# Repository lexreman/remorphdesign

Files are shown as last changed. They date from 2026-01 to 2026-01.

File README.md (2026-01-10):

<div align="center">
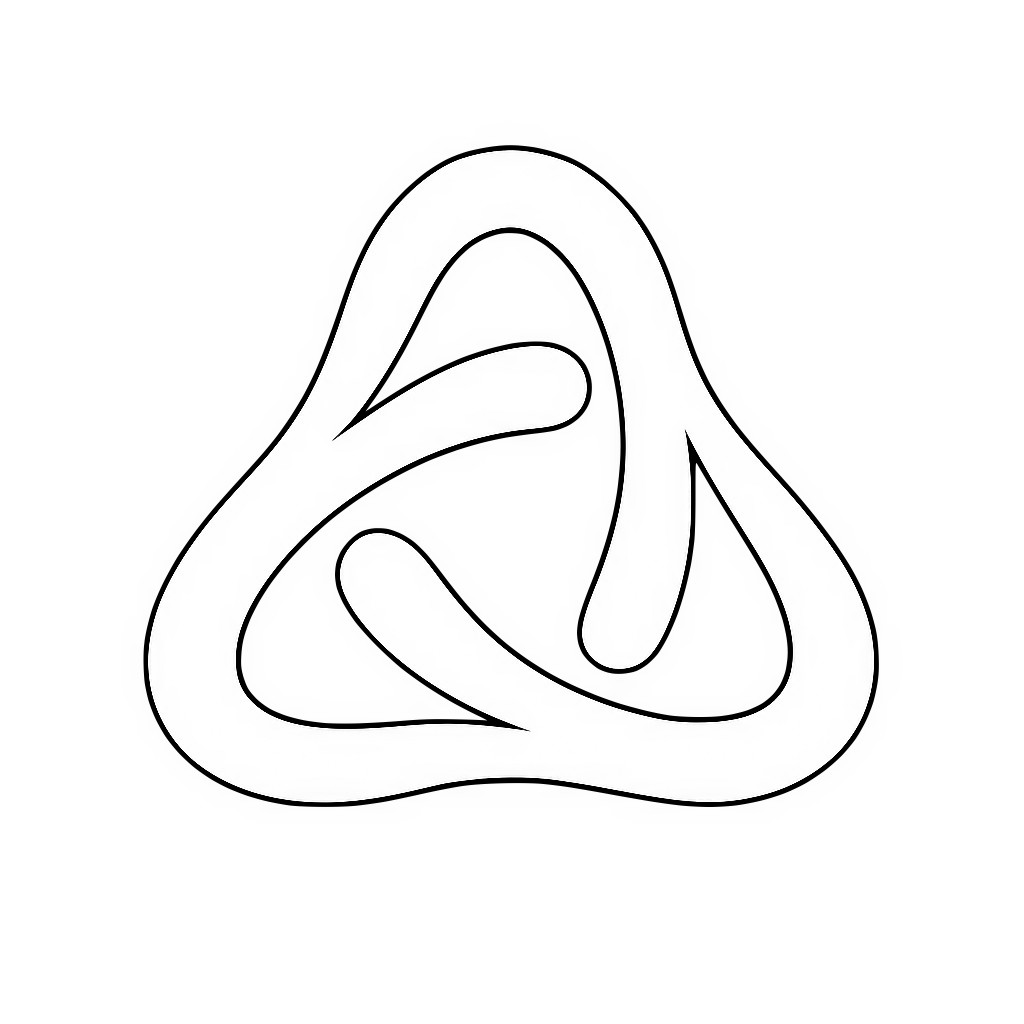
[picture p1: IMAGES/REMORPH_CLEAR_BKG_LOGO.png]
Remorph Logo


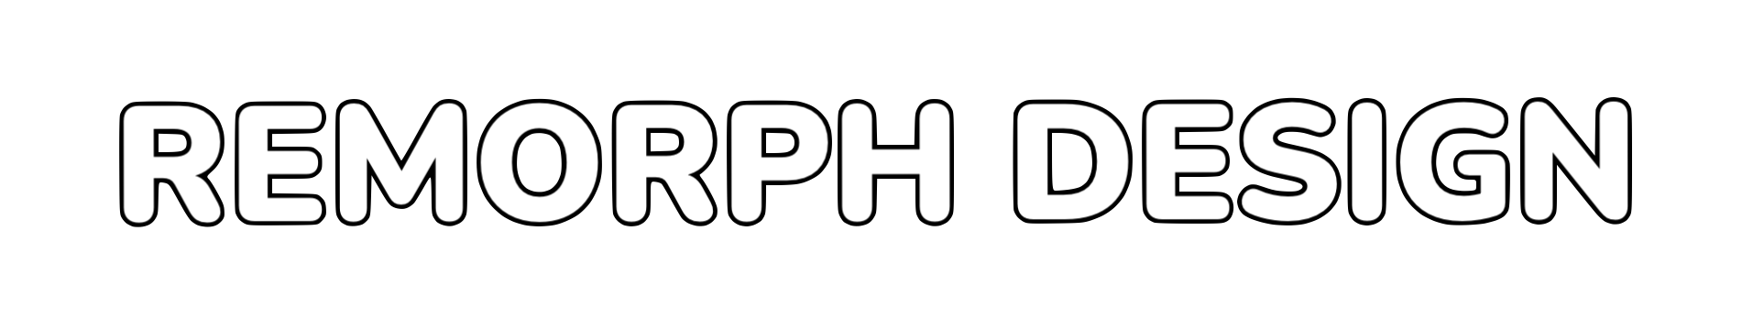
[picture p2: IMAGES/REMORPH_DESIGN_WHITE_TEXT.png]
Remorph Design Text


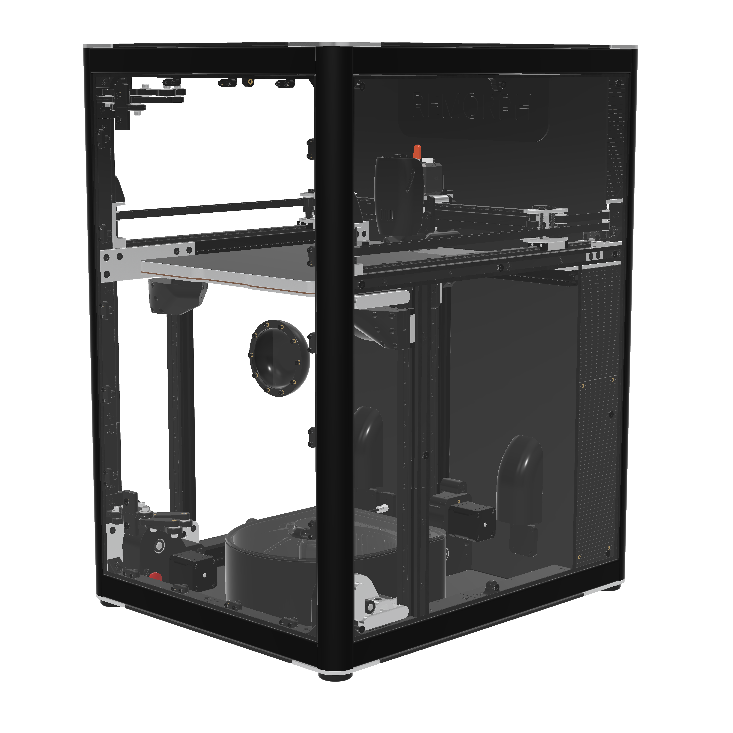
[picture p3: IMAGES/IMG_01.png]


</div>

* CPAP for print cooling and chamber convection 

* HEPA and carbon pellets with top-down convection 

* Static core XY 

* Frame made of 3030s and 2020s T-slot extrusions 

* Nearly all mechanical parts are machined aluminum 

* 48V N23 servos for X and Y 

* Servos and electronics isolated 

* 9mm belts for X Y Z 

* 12mm linear rails 

* 5:1 gear ratio for Z 

* Maxwell kinematic couplers 

* X307 Y307 Z304mm 

* W460 D560 H720mm 

* Hinges, door handle and connected cables are all internal 

* 4mm panels 

* Sealed internal filament dry box 

* External filament feed possible 

* Optical endstops 

* All idlers and gears use 5mm shafts with 13mm bearings 

* Nozzle wiper with a slide-out bucket

  **For more details, visit [www.remorphdesign.com](https://www.remorphdesign.com)**

  

<div style="display: flex; gap: 2%; flex-wrap: wrap; justify-content: flex-start;">
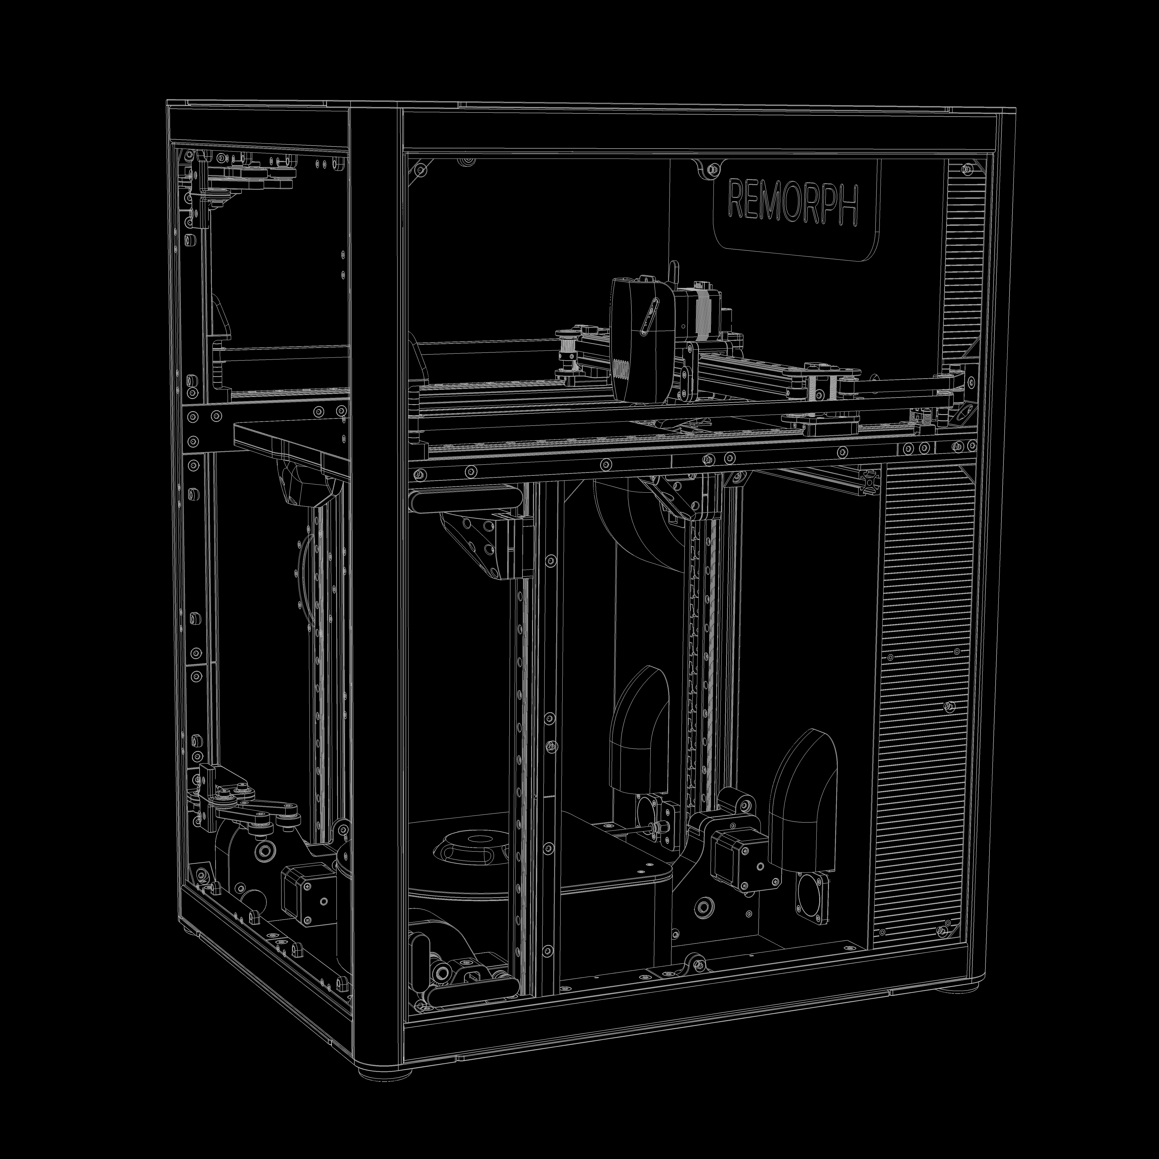
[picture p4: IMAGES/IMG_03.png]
  
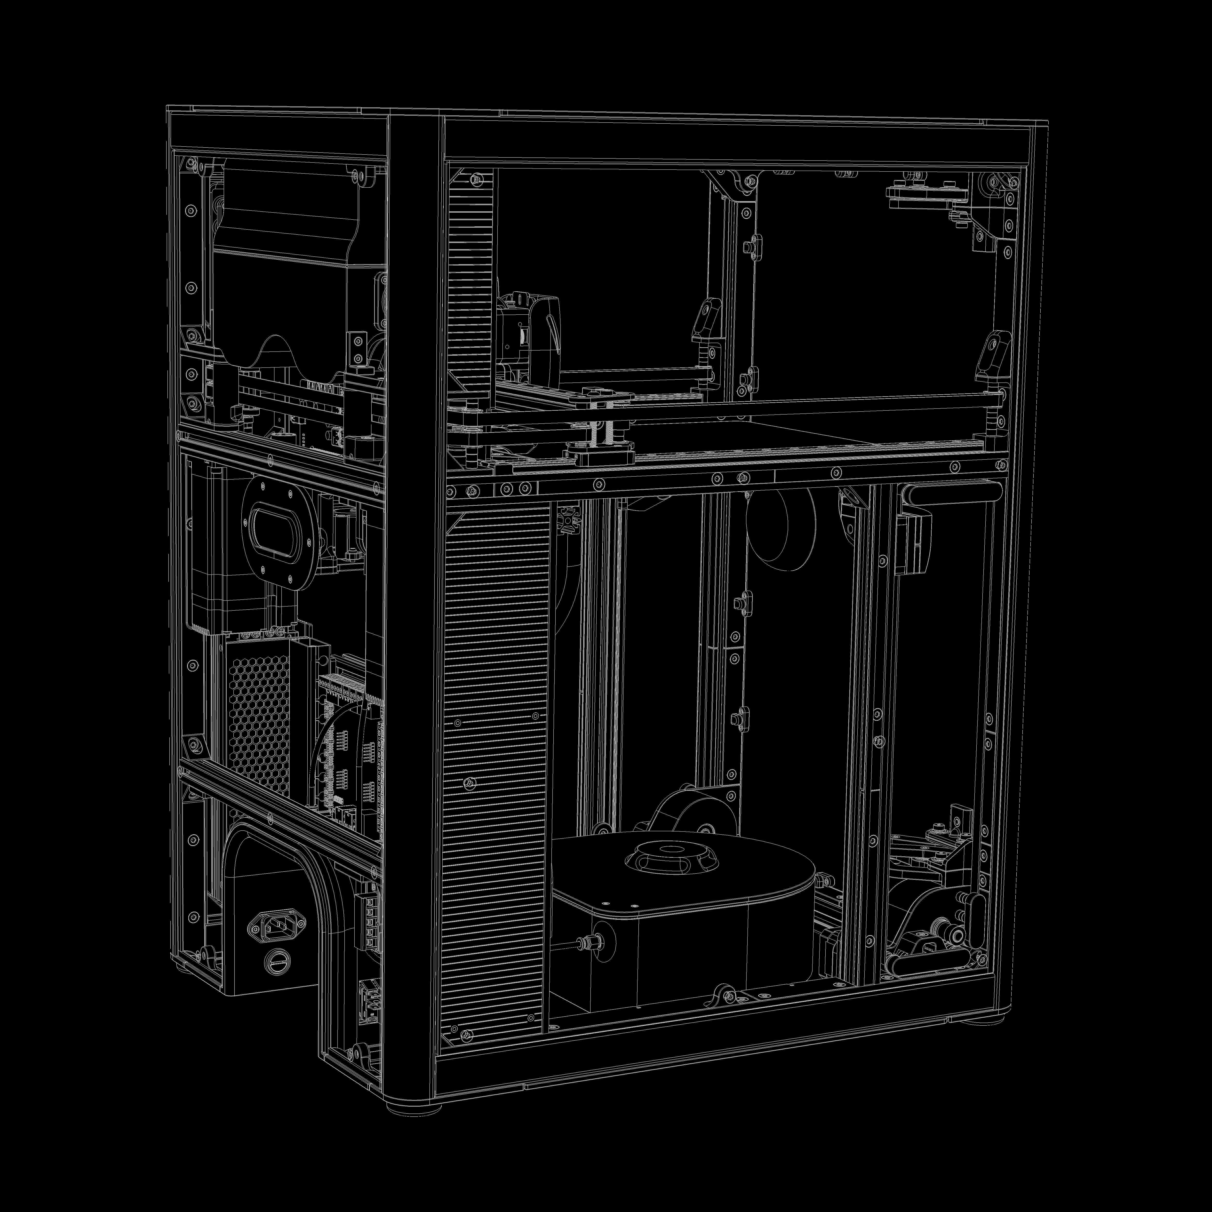
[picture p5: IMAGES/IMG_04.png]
  
</div>

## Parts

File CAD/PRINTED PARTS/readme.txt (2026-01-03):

 
 
—————————————————————————————————————————————————————————————————————— 

 1: All printed parts can fit on 250x250 plate. 
 
 2: Real ASA-CF or better, such as PPS-CF is recommended. 
 
 3: Some parts need considerably more perimeters and infill percentage. 
 
 4: Some parts have been designed with infill as filters. 
 
 5: Some parts require excellent short bridges capabilities. 
 
 6: Very few parts require support. 
 
 7: For great aesthetics, check cad assembly for part orientation, 
    and paint seam at unlikely seen position once installed. 

 ——————————————————————————————————————————————————————————————————————

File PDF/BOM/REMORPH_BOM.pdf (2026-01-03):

# REMORPH DESIGN

# BILL OF MATERIALS

## V_BETA_JAN26

FASTENERS: SCREWS
1 | M2.5x8 Tapping Pan Torx | 6
2 | M3x8 Socket Hex Stainless Steel Black | 50
3 | M3x40 Socket Hex Stainless Steel Black | 4
4 | M3x6 Button Torx Stainless Steel Black | 26
5 | M3x10 Button Torx Stainless Steel Black | 25
6 | M3x14 Button Torx Stainless Steel Black | 24
7 | M3x20 Button Torx Stainless Steel Black | 15
8 | M3x6 Flat Torx Stainless Steel Black | 54
9 | M3x10 Flat Torx Stainless Steel Black | 214
10 M3x14 Flat Torx Stainless Steel Black | 37
11 | M3x20 Flat Torx Stainless Steel Black | 26
12 M3x30 Flat Torx Stainless Steel Black | 7
13 | M3x45 Flat Torx Stainless Steel Black | 14
14 M4 ⌀5x10 Shoulder Screw | 14
15 | M5x10 Headless Hex | 2
16 M5x20 Hex Bolt Stainless Steel Black | 2
17 | M5x12 Socket Hex Stainless Steel Black | 8
18 M5 ⌀6x55 Shoulder Screw | 4
19 | M5x8 Button Torx Stainless Steel Black | 24
20 M5x10 Button Torx Stainless Steel Black | 56
21 | M5x14 Button Torx Stainless Steel Black | 14
22 M5x40 Button Torx Stainless Steel Black | 11
23 | M5x8 Flat Torx Stainless Steel Black | 20
24 M5x10 Flat Torx Stainless Steel Black | 156
25 | M5x12 Flat Torx Stainless Steel Black | 98
26 M5x14 Flat Torx Stainless Steel Black | 9
27 | M5x20 Flat Torx Stainless Steel Black | 6
28 M5x25 Flat Torx Stainless Steel Black | 6
29 | M5x35 Flat Torx Stainless Steel Black | 8
30 M5x40 Flat Torx Stainless Steel Black | 2
31 | M6x12 Flat Torx Stainless Steel Black | 2
32 M8 to M5 Adapter 15mm | 8
33 | M8x40 Button Torx Stainless Steel Black | 2

REMORPH B.O.M. PAGE 1 OF 4

FASTENERS: WASHERS
34 | M3x6x1 Washer Stainless Steel Black | 52
35 M5x8x0.5 Washer Stainless Steel | 8
36 | M5x8x1 Washer Stainless Steel | 90
37 M6x10x1 Washer Nylon | 20
38 | M8x16x2 Washer Steel or Aluminum Black | 14
FASTENERS: SPACERS
39 | M5x8x4 Round Spacer Black | 56
40 M5x8x5 Round Spacer Black | 27
FASTENERS: STANDOFFS
41 M3 (Tap) ⌀5x20 Standoff | 4
42 | M3 (Tap) ⌀5x25 Standoff | 8
43 M5 (Tap) ⌀8x80 Standoff | 1
FASTENERS: HEAT-SET INSERTS
44 M3x5x5 Heat Insert | 334
45 | M4x7x5 Heat Insert | 28
46 M5x8x6 Heat Insert | 22
47 | M6x9x6 Heat Insert | 6
FASTENERS: NUTS
48 | M5x2.7 Hex Nut | 1
49 M3 2020 T-Nut | 50
50 | M5 BS20 T-Nut | 32
51 M5 2020 T-Nut | 87
52 | M5 BS30 T-Nut | 24
53 M5 3030 T-Nut | 202
FRAME: JOINTS
54 90º 2020 Corner Joint | 42
FRAME: EXTRUSIONS
55 2020 T-Slot 200mm | 2
56 | 2020 T-Slot 400mm | 6
57 2020 T-Slot 450mm | 1
58 | 2020 T-Slot 500mm | 2
59 3030 T-Slot 400mm | 1
60 | 3030 N1 T-Slot 400mm | 3
61 3030 N1 T-Slot 500mm | 4
62 | 3030R T-Slot 700mm | 4

MOTION: BEARINGS
63 | Ball Bearing F698 | 11
64 Ball Bearing 695 | 43
65 | Ball Bearing F695 | 90
MOTION: SHAFTS
66 | 5x20 Shaft | 5
67 5x25 Shaft | 15
68 | 5x35 Shaft | 3
69 5x40 Shaft | 10
70 | 5x65 Shaft | 6
71 8x65 Shaft with Flat Side (D Type) | 5
MOTION: LINEAR RAILS
72 MGN12H 400 | 4
73 | MGN12H 450 | 2
MOTION: GEARS
74 | 2GT 16T B5 Pulley for 9mm Belt | 3
75 2GT 20T B5 Pulley for 9mm Belt (Black) | 2
76 | 2GT 20T B8 Pulley for 9mm Belt (Black) | 5
77 2GT 80T B8 Pulley for 9mm Belt | 3
MOTION: BELTS
78 9mm 2GT3 6897mm (8000mm Recommended) | 1
79 | Closed Loop 9mm 2GT2 210mm | 3
MOTION: SHAFT COUPLERS
80 | GND GTC 19x26 8x8 or 8 to 8mm Shaft Coupler (⌀21x31mm MAX) | 2
MOTION: BALL JOINTS
81 | M5 12mm Magnetic Steel Ball | 3
MOTORS
82 | OMC ISV57T-180S or N23 146mm MAX | 2
83 N17 48 or 60mm MAX | 3
ELECTRONICS: FANS
84 ASB02505SHA-AY6B or 10x25mm Axial Fan | 1
85 | WS7040-24 with controller | 2
86 9BMC24P2G001 | 1
ELECTRONICS: POWER SUPPLIES
87 LCW15US05 | 1
88 | UHP-500-24 | 1
89 UHP-500-48 | 1

ELECTRONICS: CONNECTORS
90 | Degson 6p Set 15EDGKM-3.81-06P + 15CDGV-3.81-06P | 9
91 Wago 221-415 | 3
92 | AC Inlet IEC 320-C14 15GEEG3E | 1
93 Fuse Holder SCHURTER 0031.2207 | 1
ELECTRONICS: SWITCHES
94 Rocker Switch Bulgin C6050ALBR-1197W | 1
95 | 16mm Panel Flat Push Button | 1
96 16mm Red Mushroom Button | 2
ELECTRONICS: SENSORS
97 M3 PT1000 | 3
98 | OPTEK OPB990T51Z | 2
99 BEACON LP | 1
100 | BME680 Adafruit 3660 | 1
101 BTT SFS 2 | 1
ELECTRONICS: PCBS
102 Recore A8 | 1
103 | BTT EBB42 | 2
104 RPI USB 3.2 HUB HAT | 1
105 | Matek Mini Hub | 1
MISCELLANEOUS
106 | TE Connectivity Potter SSRMP-240D16R | 2
107 LED COB 24V 7W ⌀20mm | 1
108 | PC4-M6 | 7
109 3x5mm 2.3m EVA Strip (3m Recommended) | 1
110 | 1x5mm 20.2m EVA Strip (22m Recommended) | 1
111 ⌀6mm Sealing Rope 820.4mm (vacuum table) | 1
112 | CPAP Tube | 2
113 ⌀40x10 Rubber Foot | 4
114 | Filament tube 2m | 1
115 3x10x20mm Rubber for Nozzle Wipper | 1
116 | 20x40x300mm Raceway | 1
117 Nema 17 Rubber Damper 2mm | 6
118 | 10x15x25 Magnet | 3
119 ⌀5x5 Magnet | 100
120 | Printed Parts | ?
121 Milled Parts | 54
122 | PC/CF Panels | 10

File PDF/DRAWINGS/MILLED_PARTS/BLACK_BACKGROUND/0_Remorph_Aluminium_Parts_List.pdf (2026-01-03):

### REMORPH ALUMINIUM PARTS LIST

1 TCP: Top Corner Plate | 7075-T6 | 5x73x73 | 4
2 | FBCP: Front Bot Corner Plate | 7075-T6 | 5x73x73 | 2
3 LBBCP: Left Bot Back Corner Plate | 7075-T6 | 10x50x103 | 1
4 | RBBCP: Right Bot Back Corner Plate | 7075-T6 | 10x50x103 | 1
5 LFZDM: Left Front Z Drive Mount | 7075-T6 | 5x97x155 | 1
6 | RFZDM: Right Front Z Drive Mount | 7075-T6 | 5x97x155 | 1
7 FTBZIM: Front Top Big Z Idler Mount | 7075-T6 | 5x41x155 | 2
8 | XYP: XY Plate | 7075-T6 | 5x139x450 | 1
9 FTLZIB: Front Top Little Z Idler Body | 7075-T6 | 8x15x89 | 2
10 | FZTB: Front Z Tensioner Body | 7075-T6 | 21x27x42 | 2
11 FBBZIB: Front Bot Big Z Idler Body | 7075-T6 | 15x25x76 | 2
12 | FBLZIB: Front Bot Little Z Idler Body | 7075-T6 | 8x15x45 | 2
13 LBZDM: Left Back Z Drive Mount | 7075-T6 | 9x54x94 | 1
14 | RBZDM: Right Back Z Drive Mount | 7075-T6 | 9x54x94 | 1
15 BZTB: Back Z Tensioner Body | 7075-T6 | 16x22x28 | 1
16 | BZPP: Back Z Puller Plate | 7075-T6 | 5x16x30 | 1
17 BZIM: Back Z Idler Mount | 7075-T6 | 25x29x75 | 1
18 | XYBTM: XY Bot Tensioner Mount | 7075-T6 | 5x69x112 | 2
19 XYTTM: XY Top Tensioner Mount | 7075-T6 | 5x65x112 | 2
20 | FZYTLB: First XY Tensioner Lever Body | 7075-T6 | 5x24x94 | 2
21 SXYTLB: Second XY Tensioner Lever Body | 7075-T6 | 5x24x94 | 2
22 | XYTPB: XY Tensioner Puller Body | 7075-T6 | 15x23x30 | 2
23 TBB: Tensioner Bracket Body | 7075-T6 | 4x22x80 | 2
24 | LYSB: Left Y Stopper Body | 7075-T6 | 9x28x35 | 2
25 RYSB: Right Y Stopper Body | 7075-T6 | 9x28x35 | 2
26 | LXYIM: Left XY Idler Mount | 7075-T6 | 23x25x58 | 1
27 RXYIM: Right XY Idler Mount | 7075-T6 | 23x25x58 | 1
28 | LBXYJB: Left Bot XY Joint Body | 7075-T6 | 10x54x60 | 1
29 RBXYJB: Right Bot XY Joint Body | 7075-T6 | 10x54x60 | 1
30 | LMXYJB: Left Middle XY Joint Body | 7075-T6 | 18x20x32 | 1
31 RMXYJB: Right Middle XY Joint Body | 7075-T6 | 18x20x32 | 1
32 | TXYJB: Top XY Joint Body | 7075-T6 | 4x24x62 | 2
33 TP: Toolhead Plate | 7075-T6 | 9x66x99 | 1
34 | LM: LED MOUNT | 7075-T6 | 10x50x75 | 1
35 RRTM: RAPIDO REMORPH Toolhead Mount | 7075-T6 | 5x43x43 | 1
36 | CRTS: CHUBE REMORPH Toolhead Spacer | 7075-T6 | 2x26x26 | 1 Total 54

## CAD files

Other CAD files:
CAD/ASSEMBLY/REMORPH_DESIGN_BETA_1.step
CAD/MILLED PARTS/13_Left_Back_Z_Drive_Mount.step
CAD/PC PANELS/8_Back_Panel.step
CAD/MILLED PARTS/5_Left_Front_Z_Drive_Mount.step
CAD/PC PANELS/10_Filament_Dry_Box_Lid.step
CAD/MILLED PARTS/27_Right_XY_Idler_Mount.step
CAD/PC PANELS/5_Top_Panel.step
CAD/MILLED PARTS/12_Front_Bot_Little_Z_Idler_Body.step
CAD/PC PANELS/4_Rear_Connectors_Recess_Panel.step
CAD/MILLED PARTS/17_Back_Z_Idler_Mount.step
CAD/PC PANELS/1_Inside_Bot_Panel.step
CAD/MILLED PARTS/29_Right_Bot_XY_Joint.step
CAD/PC PANELS/7_Right_Panel.step
CAD/MILLED PARTS/3_Left_Bot_Back_Corner_Plate.step
CAD/PC PANELS/2_Inside_Top_Panel.step
CAD/MILLED PARTS/18_XY_Bot_Tensioner_Mount.step
CAD/PC PANELS/9_Front_Panel.step
CAD/MILLED PARTS/30_Left_Middle_XY_Joint_Body.step
CAD/ASSEMBLY/REMORPH_DESIGN_BETA_1.x_t
CAD/MILLED PARTS/10_Front_Z_Tensioner_Body.step
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

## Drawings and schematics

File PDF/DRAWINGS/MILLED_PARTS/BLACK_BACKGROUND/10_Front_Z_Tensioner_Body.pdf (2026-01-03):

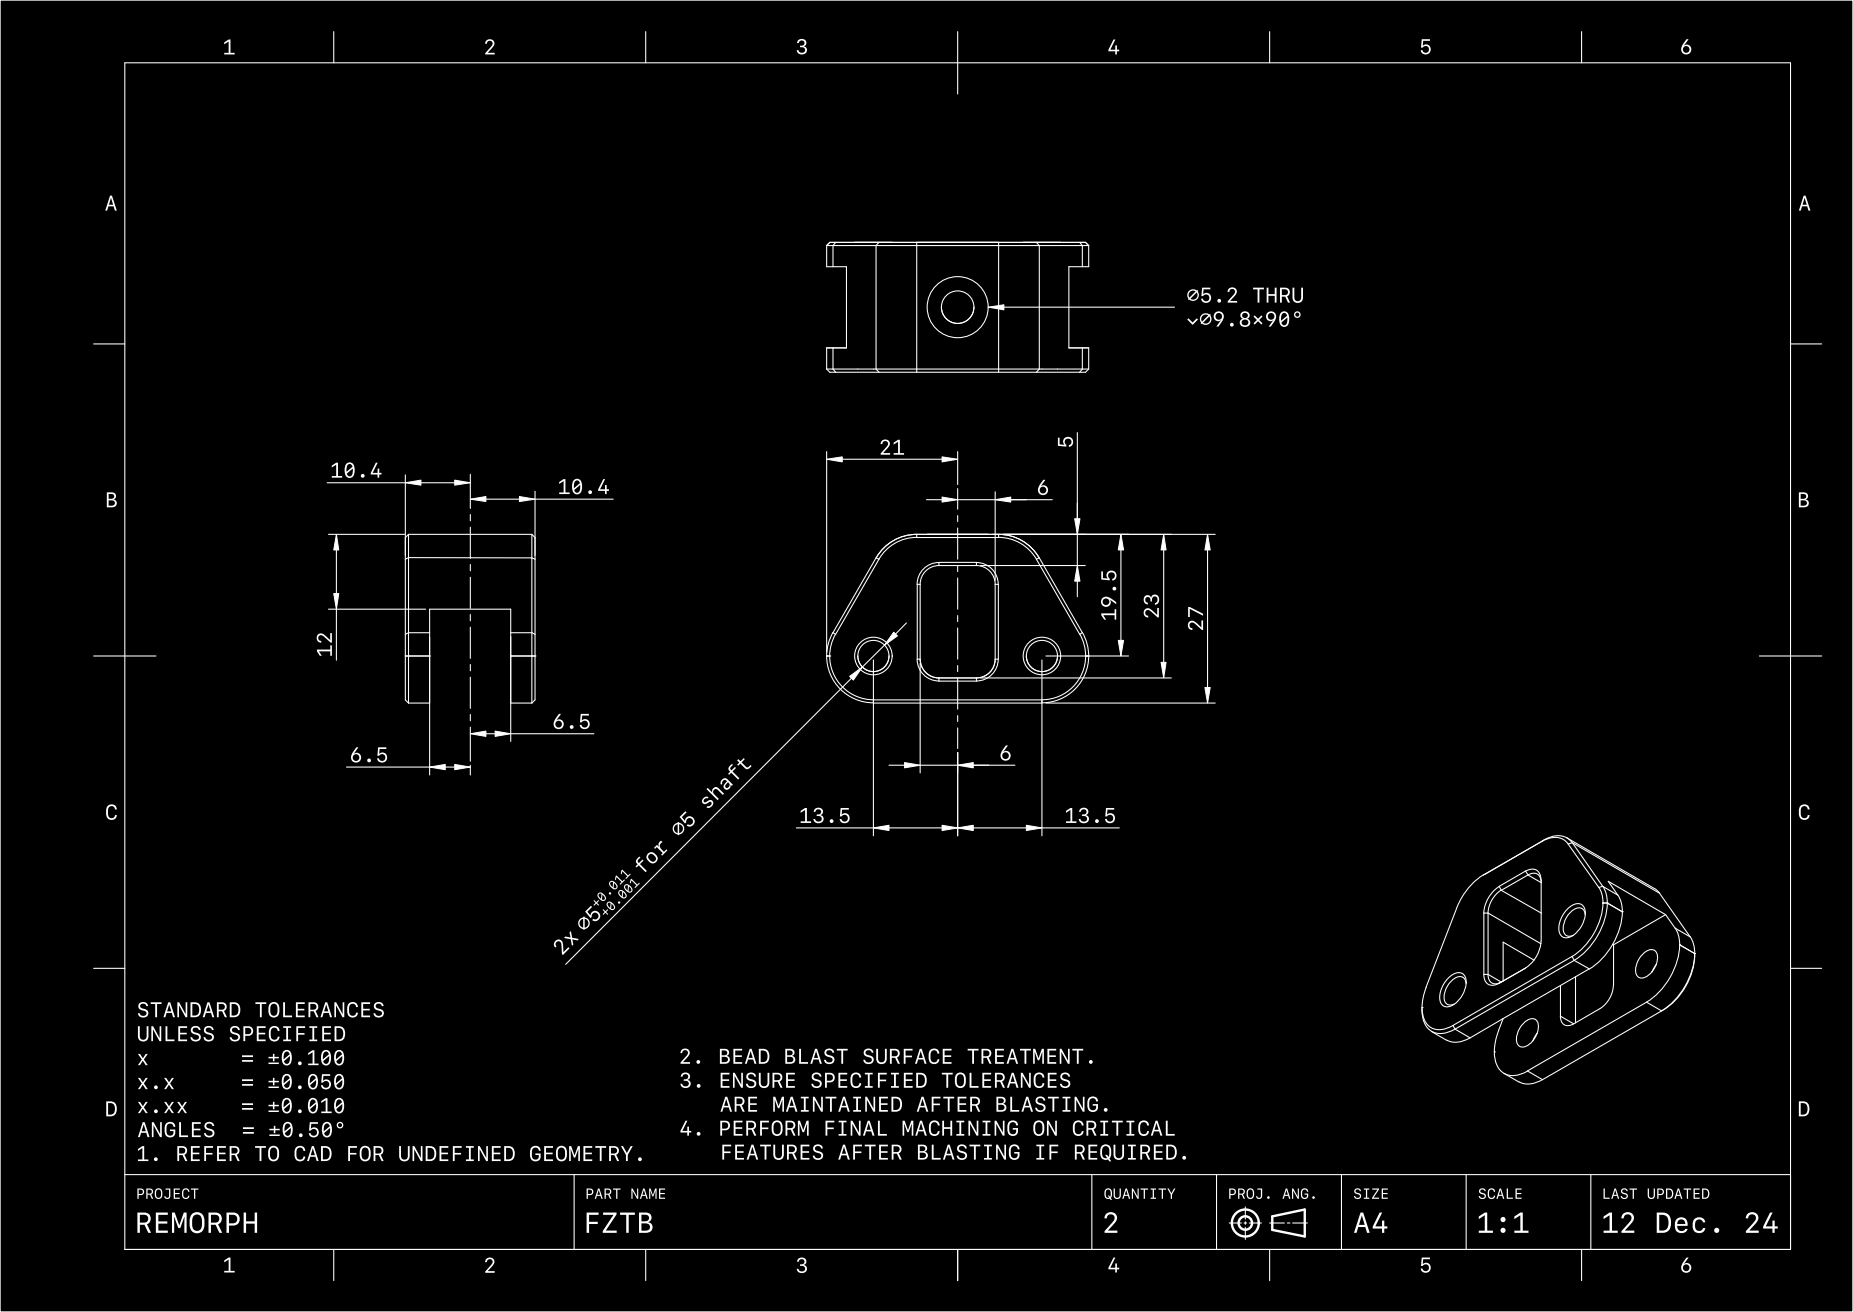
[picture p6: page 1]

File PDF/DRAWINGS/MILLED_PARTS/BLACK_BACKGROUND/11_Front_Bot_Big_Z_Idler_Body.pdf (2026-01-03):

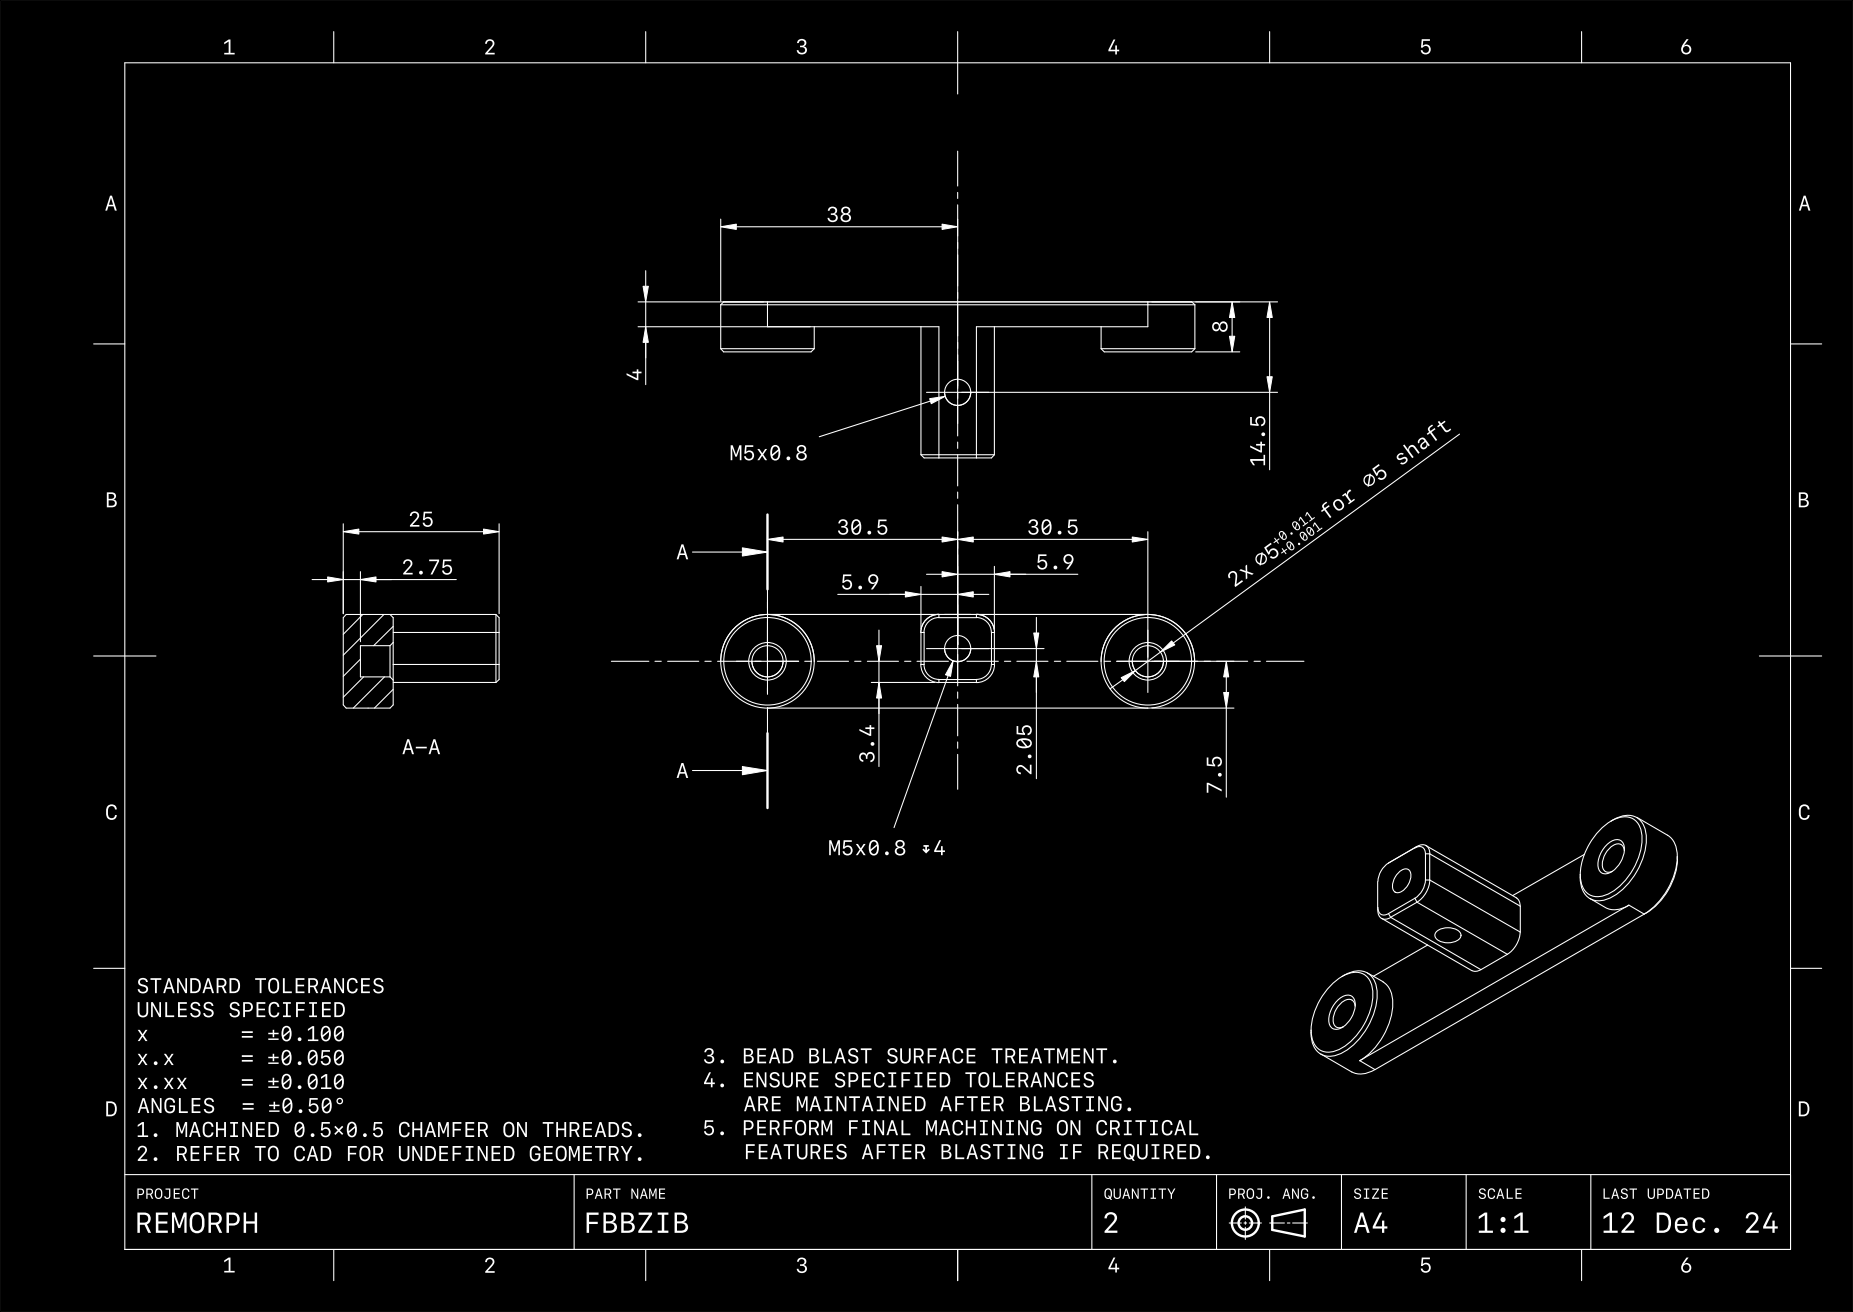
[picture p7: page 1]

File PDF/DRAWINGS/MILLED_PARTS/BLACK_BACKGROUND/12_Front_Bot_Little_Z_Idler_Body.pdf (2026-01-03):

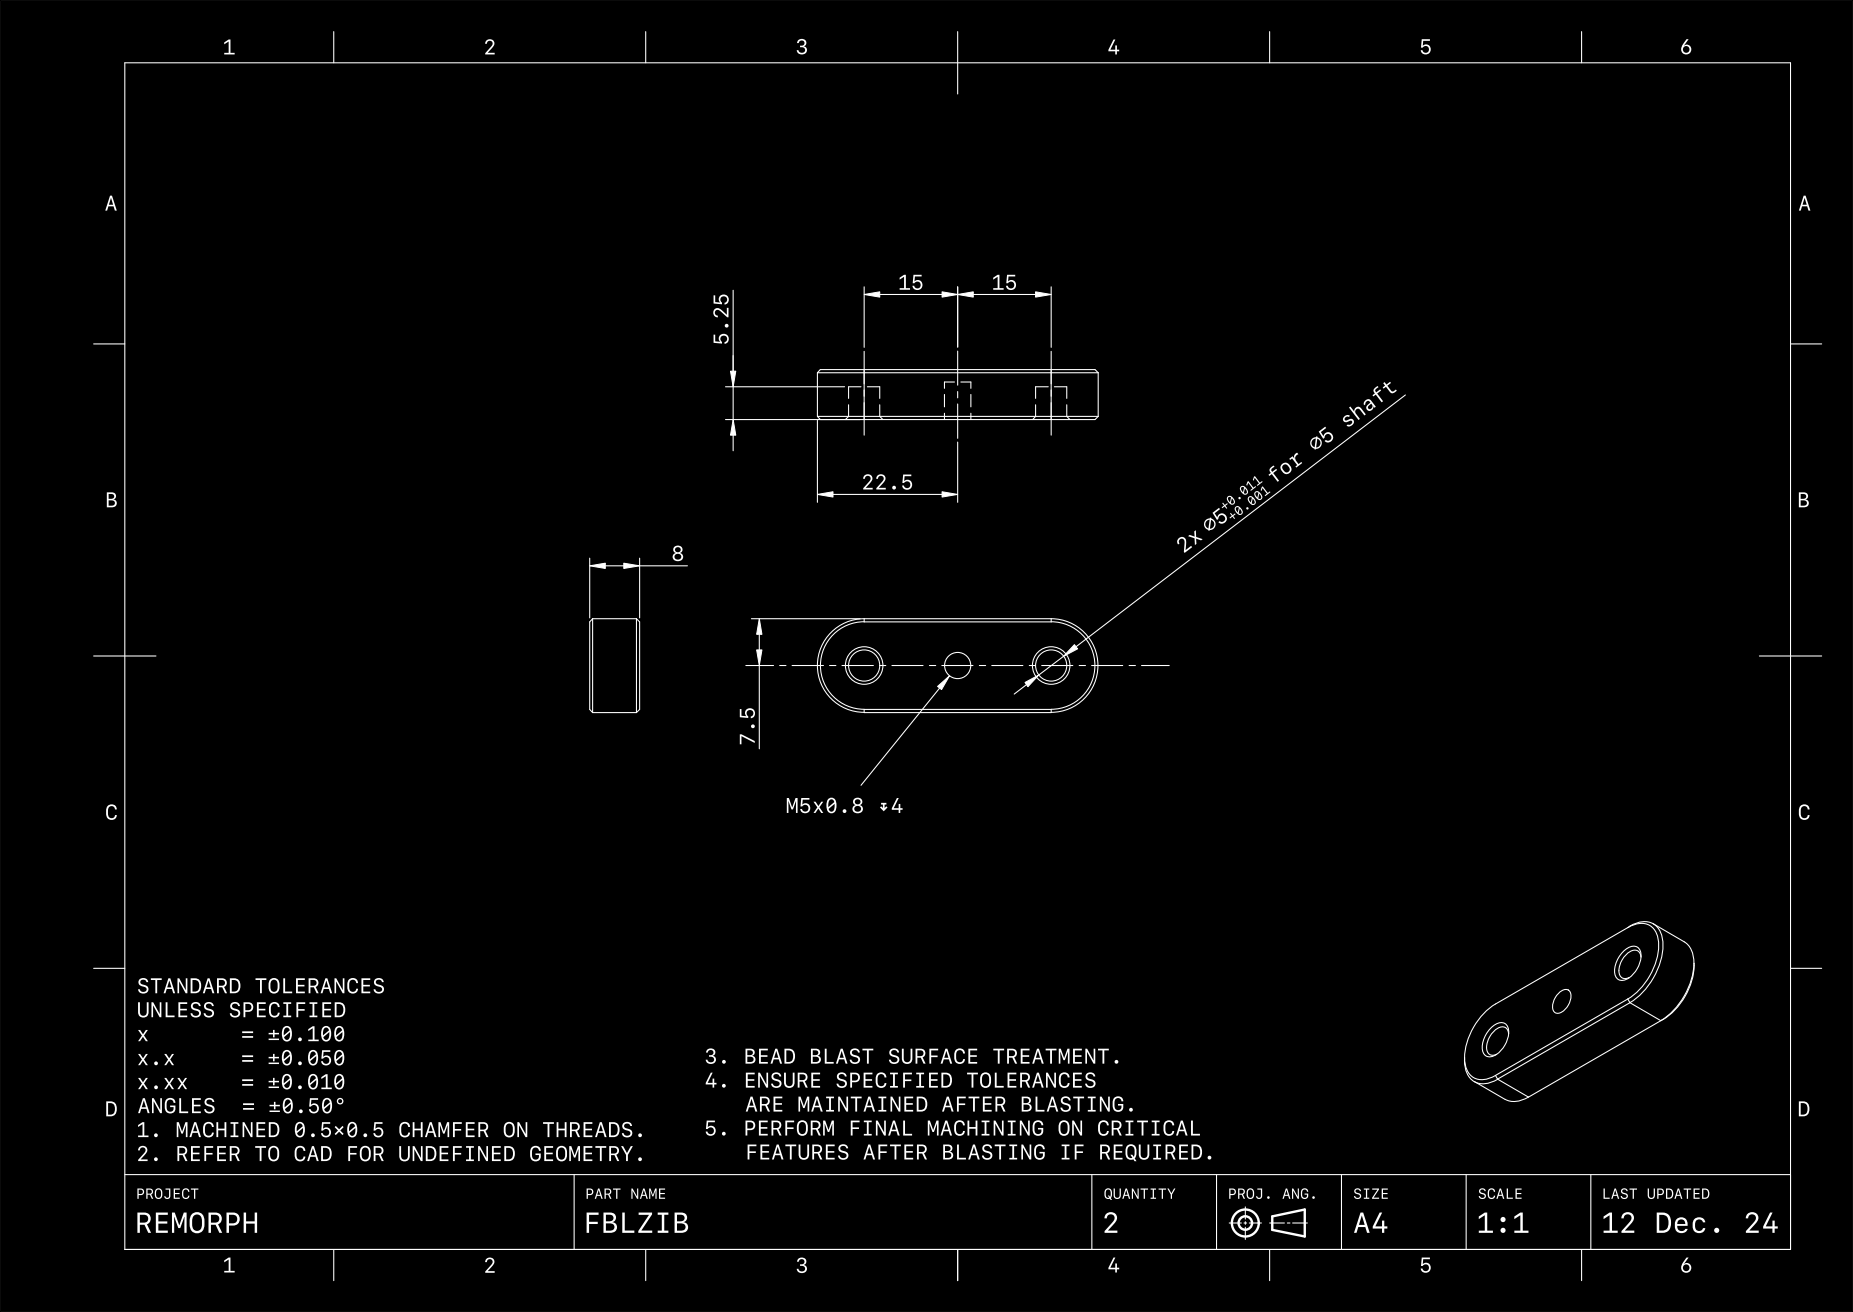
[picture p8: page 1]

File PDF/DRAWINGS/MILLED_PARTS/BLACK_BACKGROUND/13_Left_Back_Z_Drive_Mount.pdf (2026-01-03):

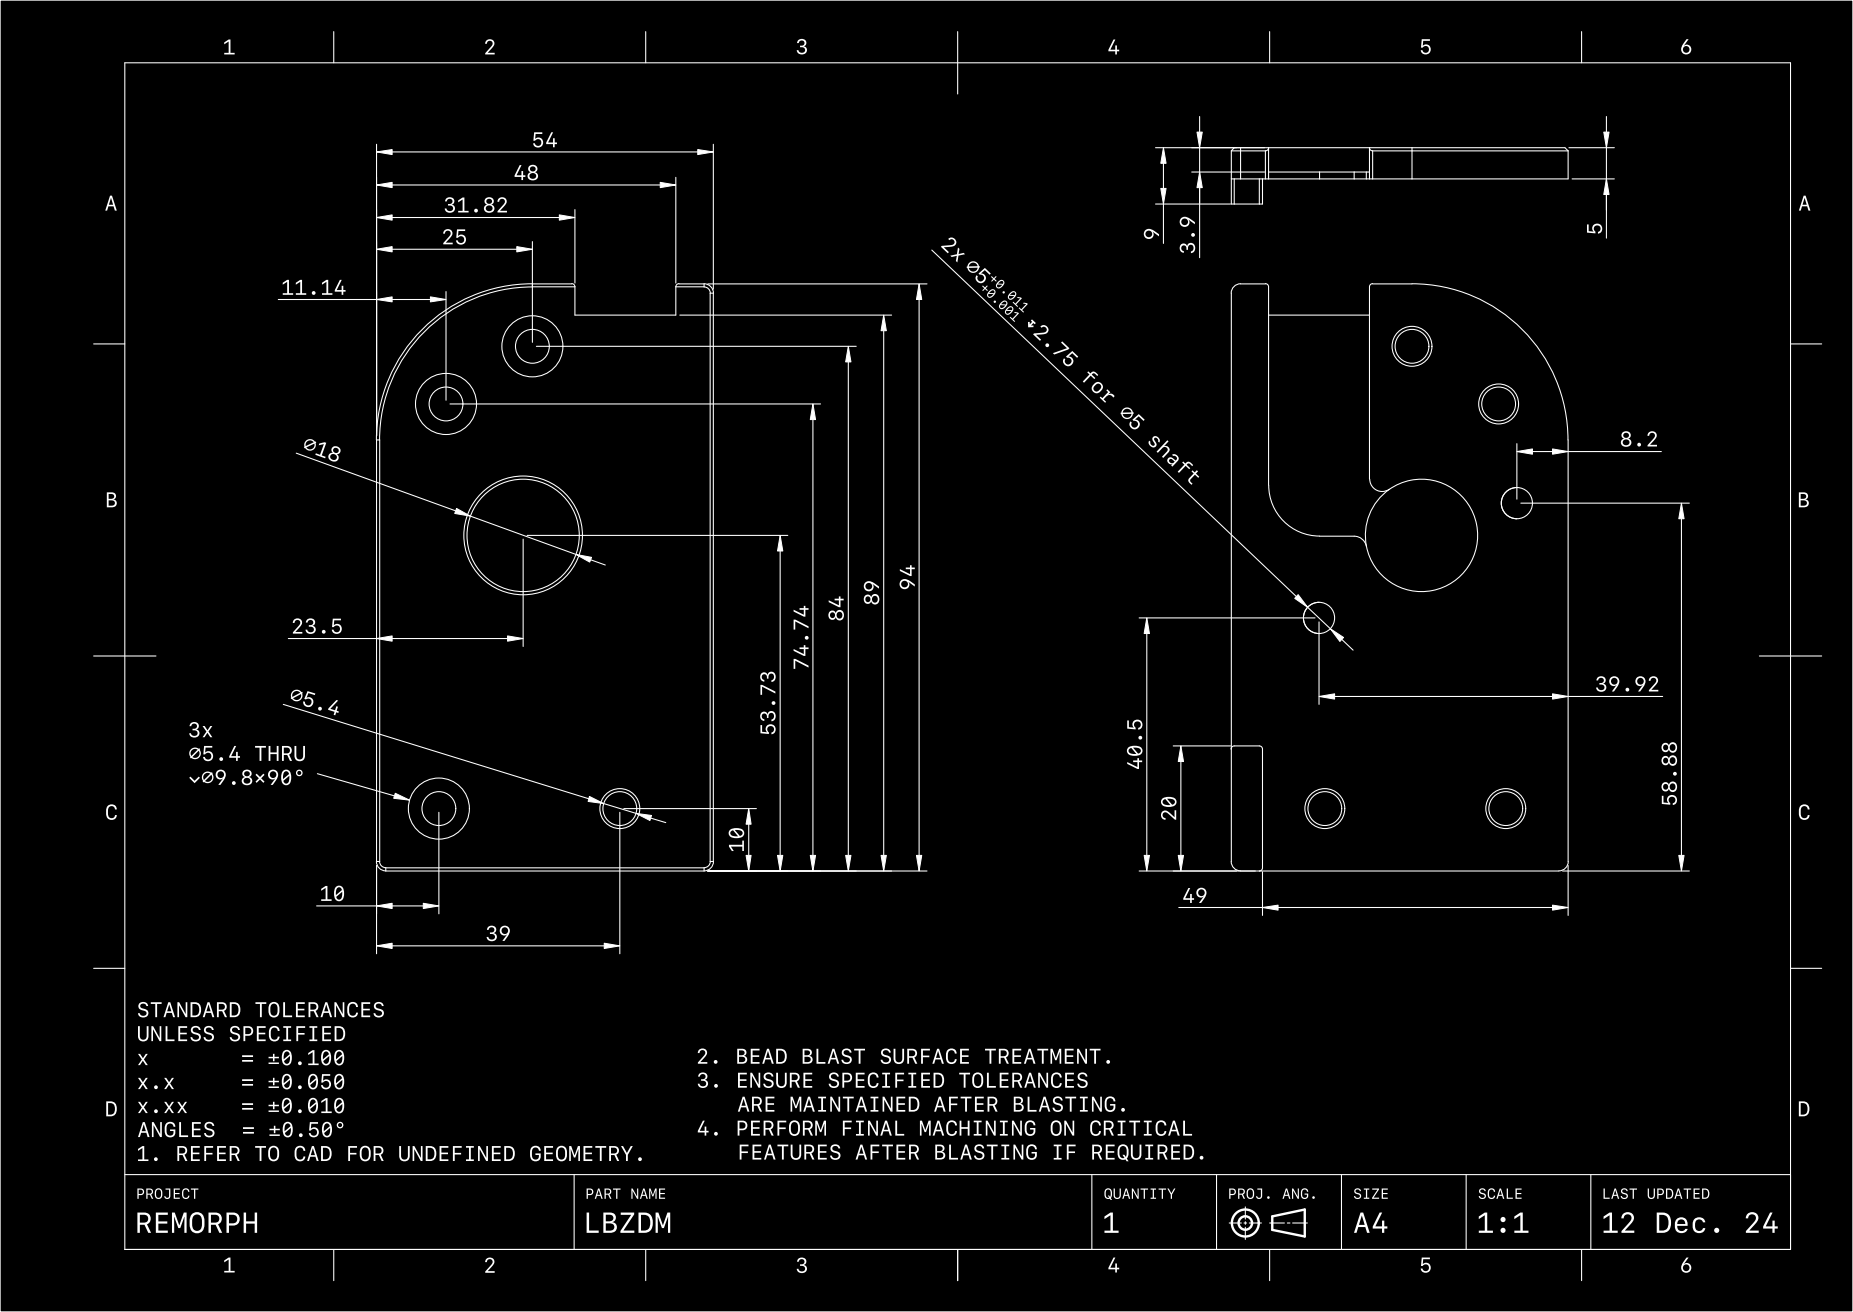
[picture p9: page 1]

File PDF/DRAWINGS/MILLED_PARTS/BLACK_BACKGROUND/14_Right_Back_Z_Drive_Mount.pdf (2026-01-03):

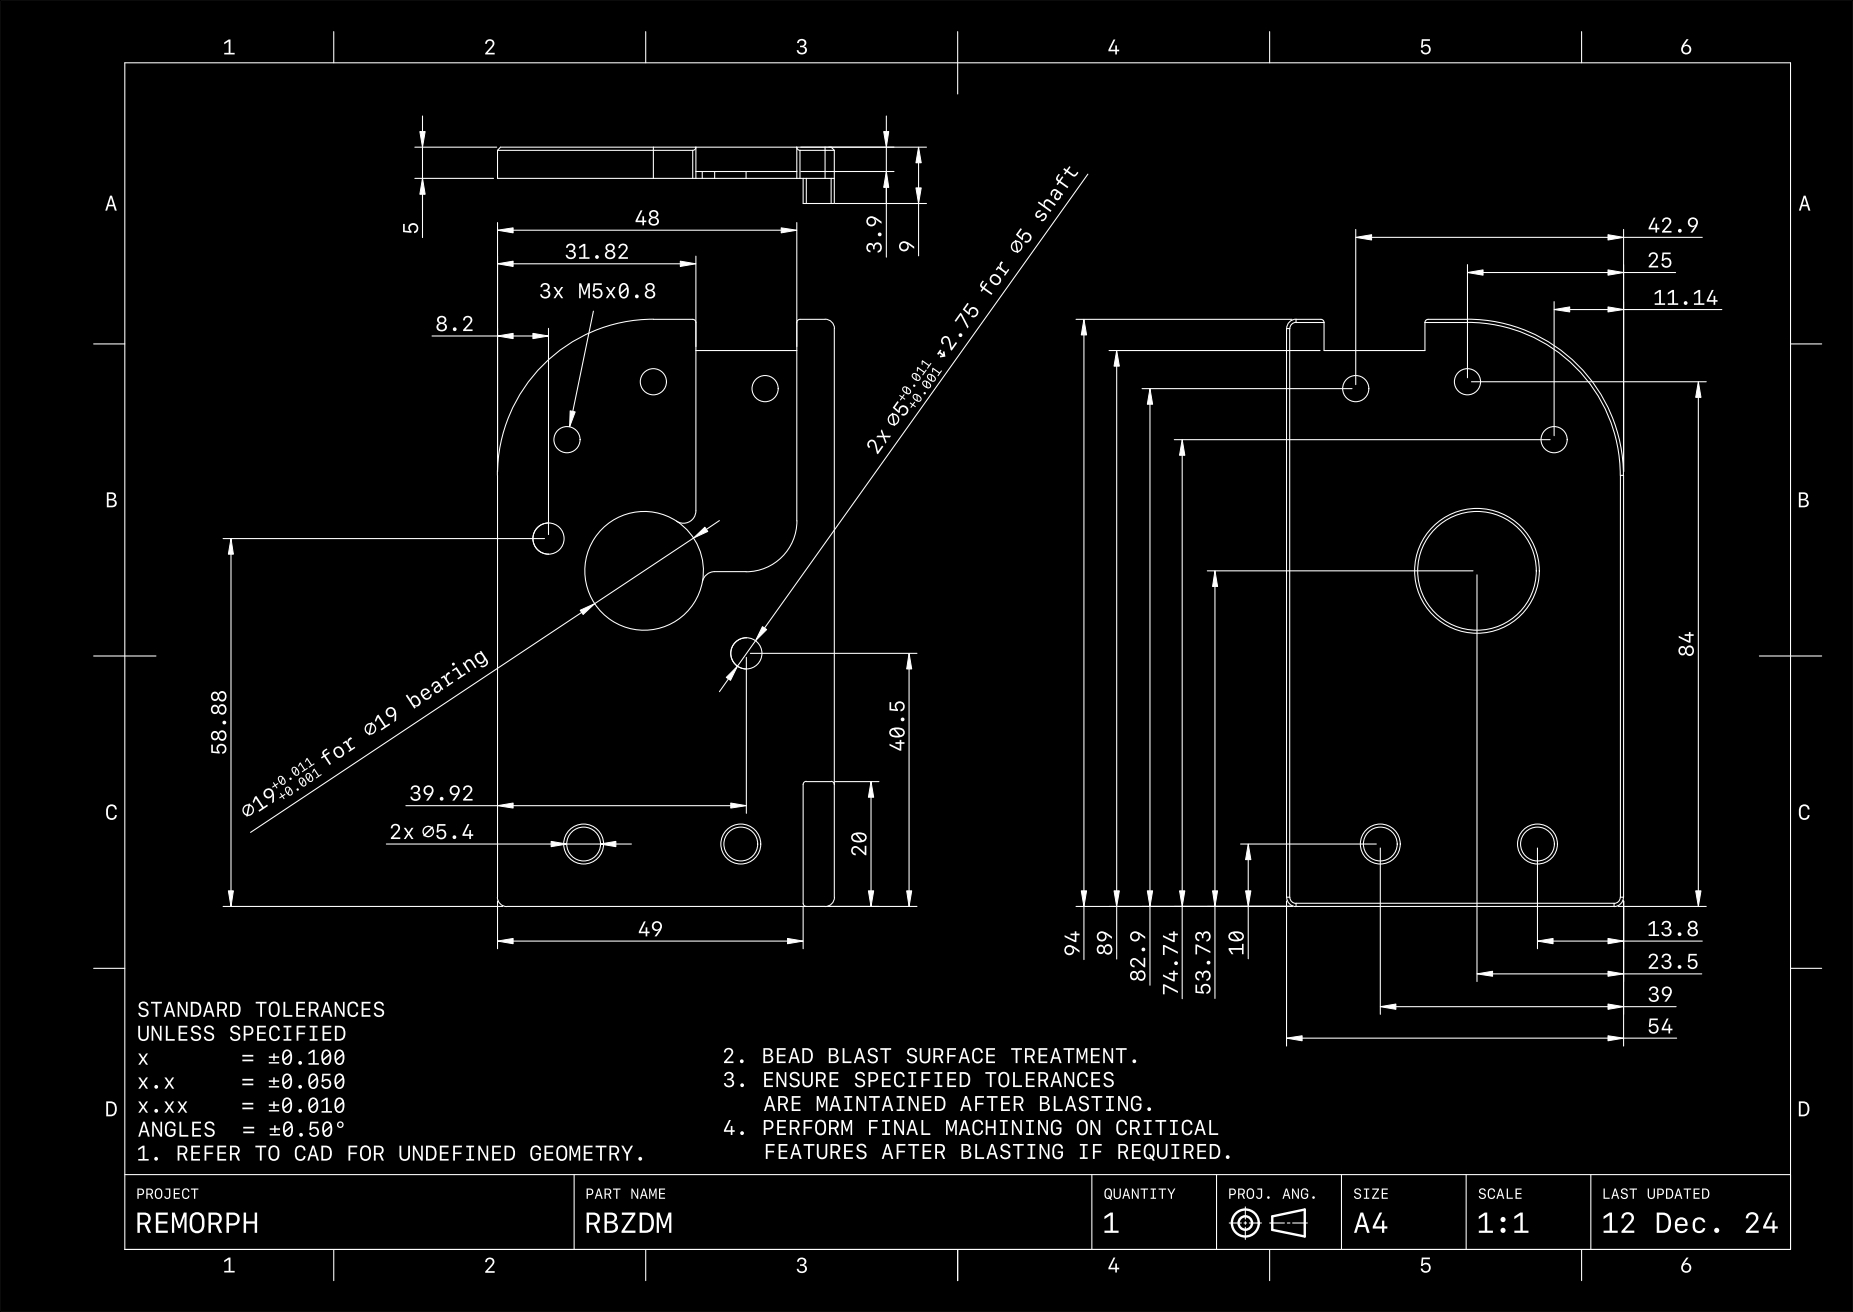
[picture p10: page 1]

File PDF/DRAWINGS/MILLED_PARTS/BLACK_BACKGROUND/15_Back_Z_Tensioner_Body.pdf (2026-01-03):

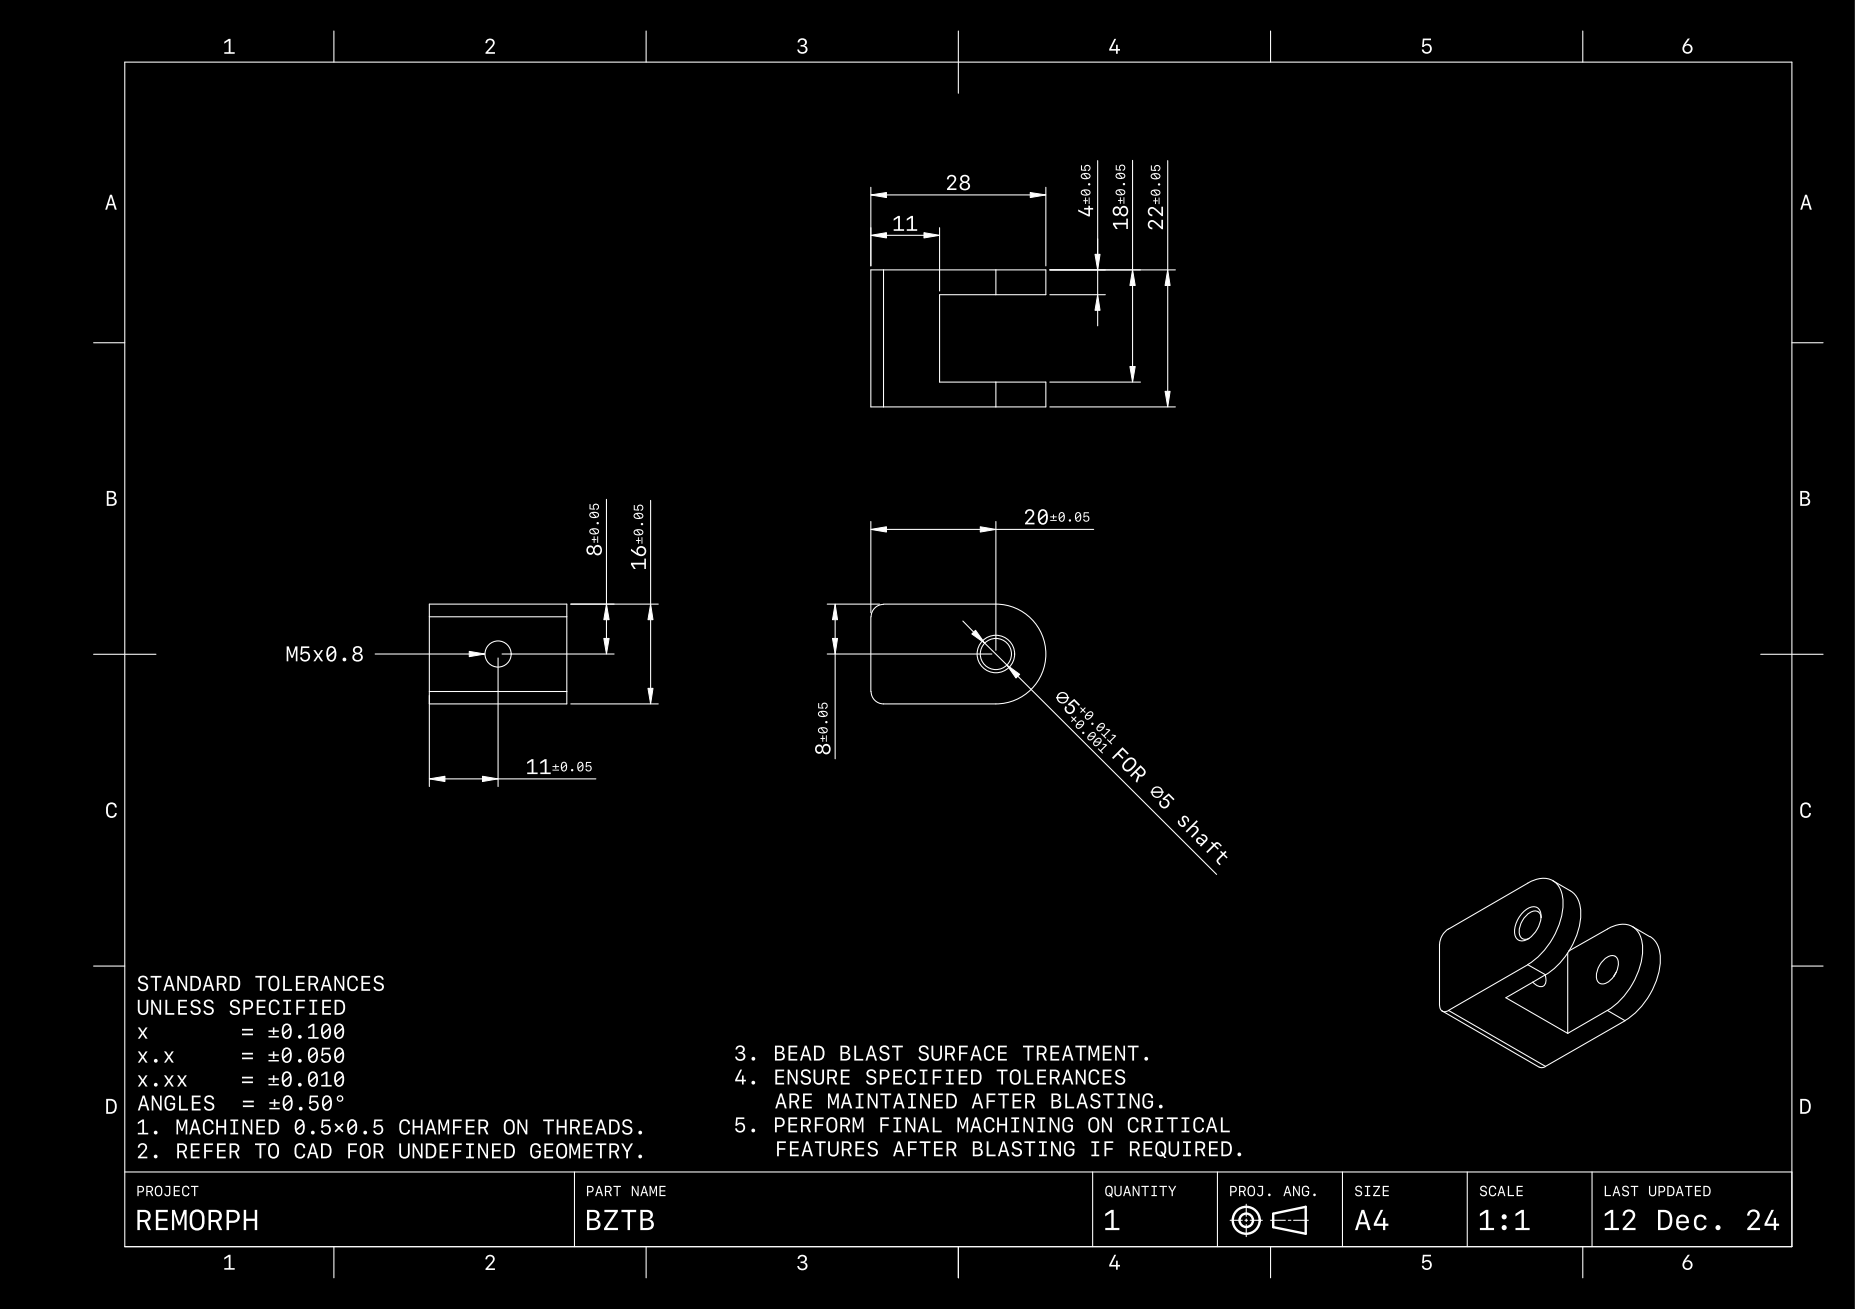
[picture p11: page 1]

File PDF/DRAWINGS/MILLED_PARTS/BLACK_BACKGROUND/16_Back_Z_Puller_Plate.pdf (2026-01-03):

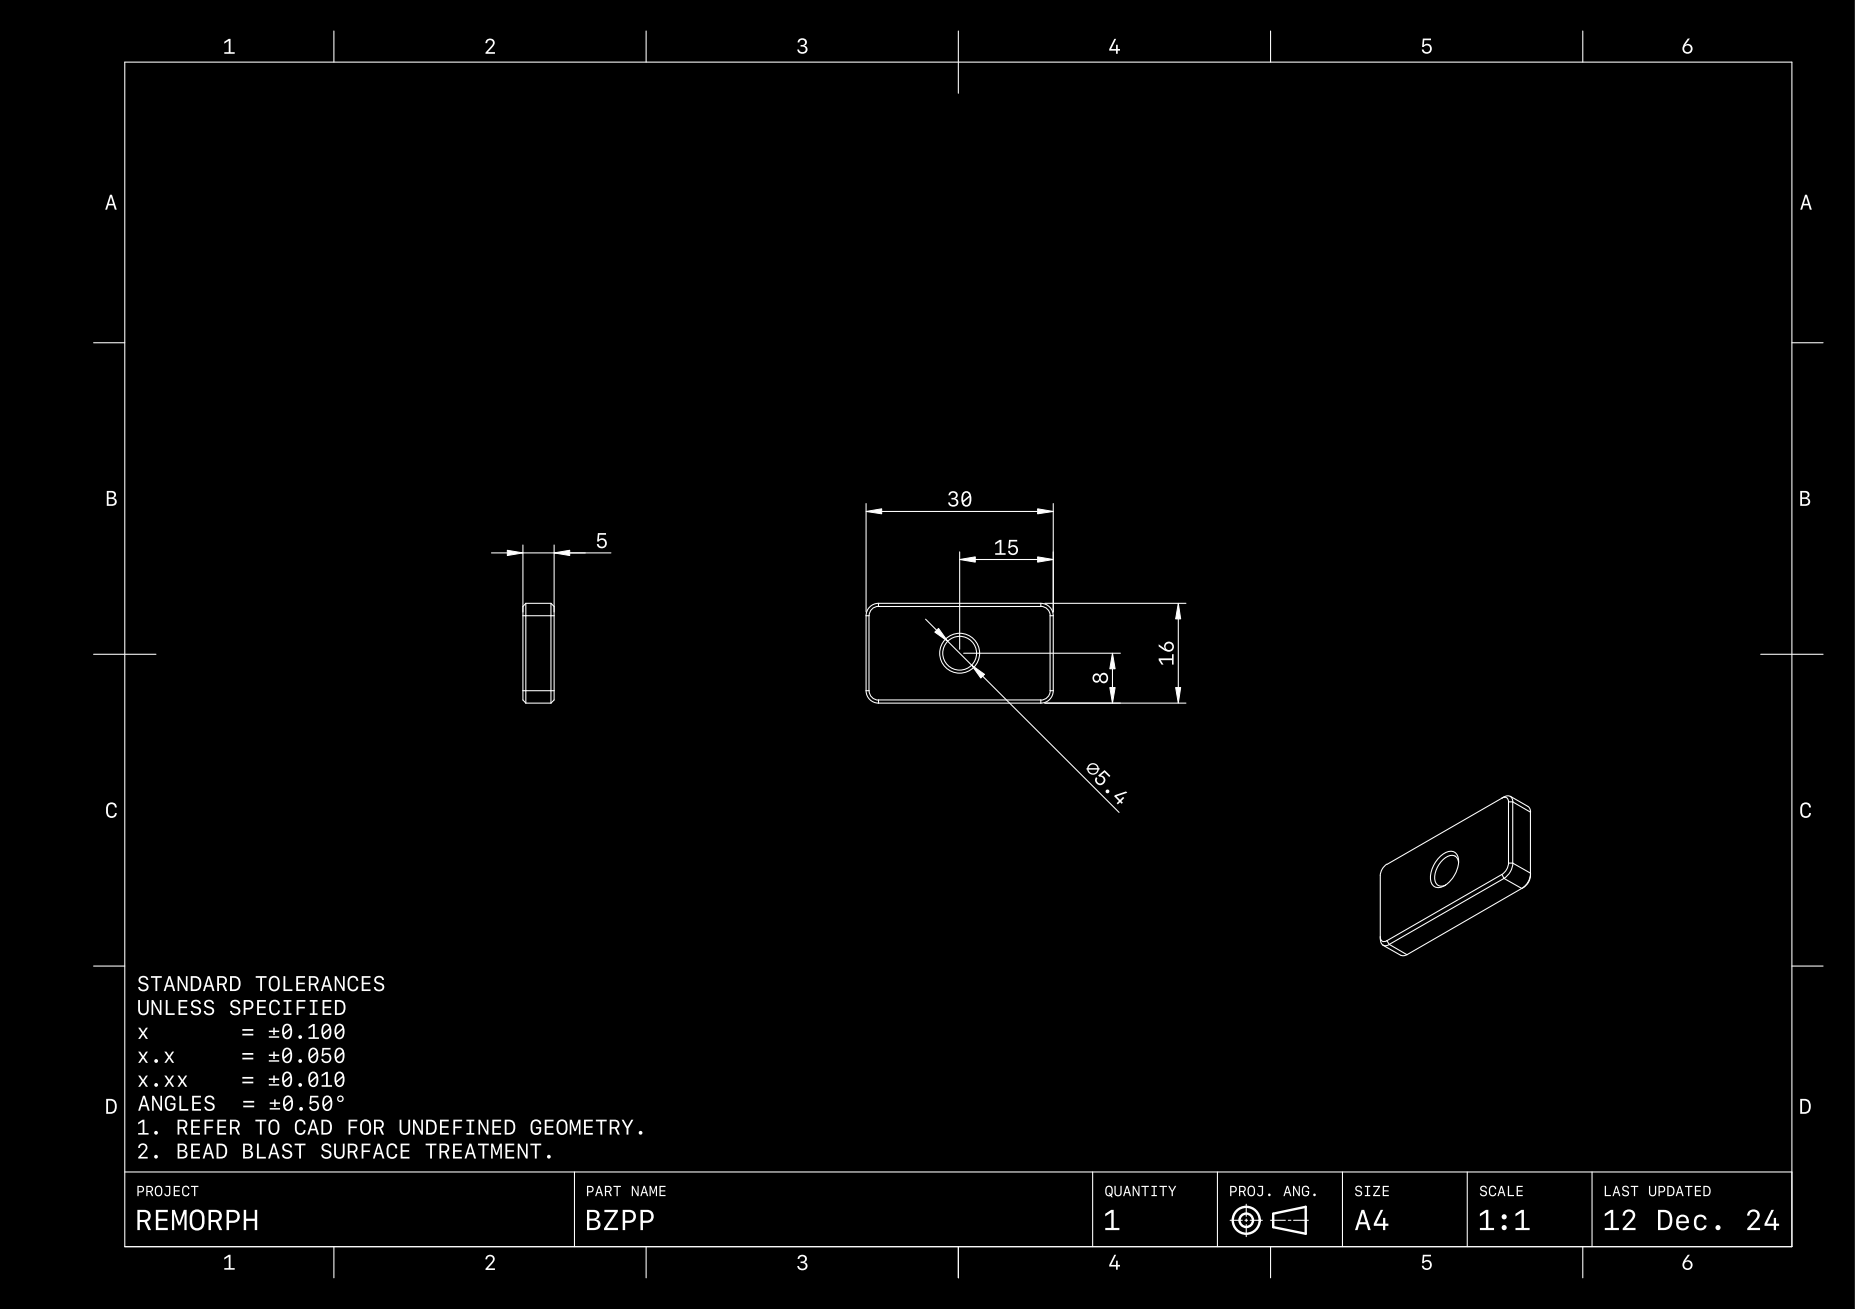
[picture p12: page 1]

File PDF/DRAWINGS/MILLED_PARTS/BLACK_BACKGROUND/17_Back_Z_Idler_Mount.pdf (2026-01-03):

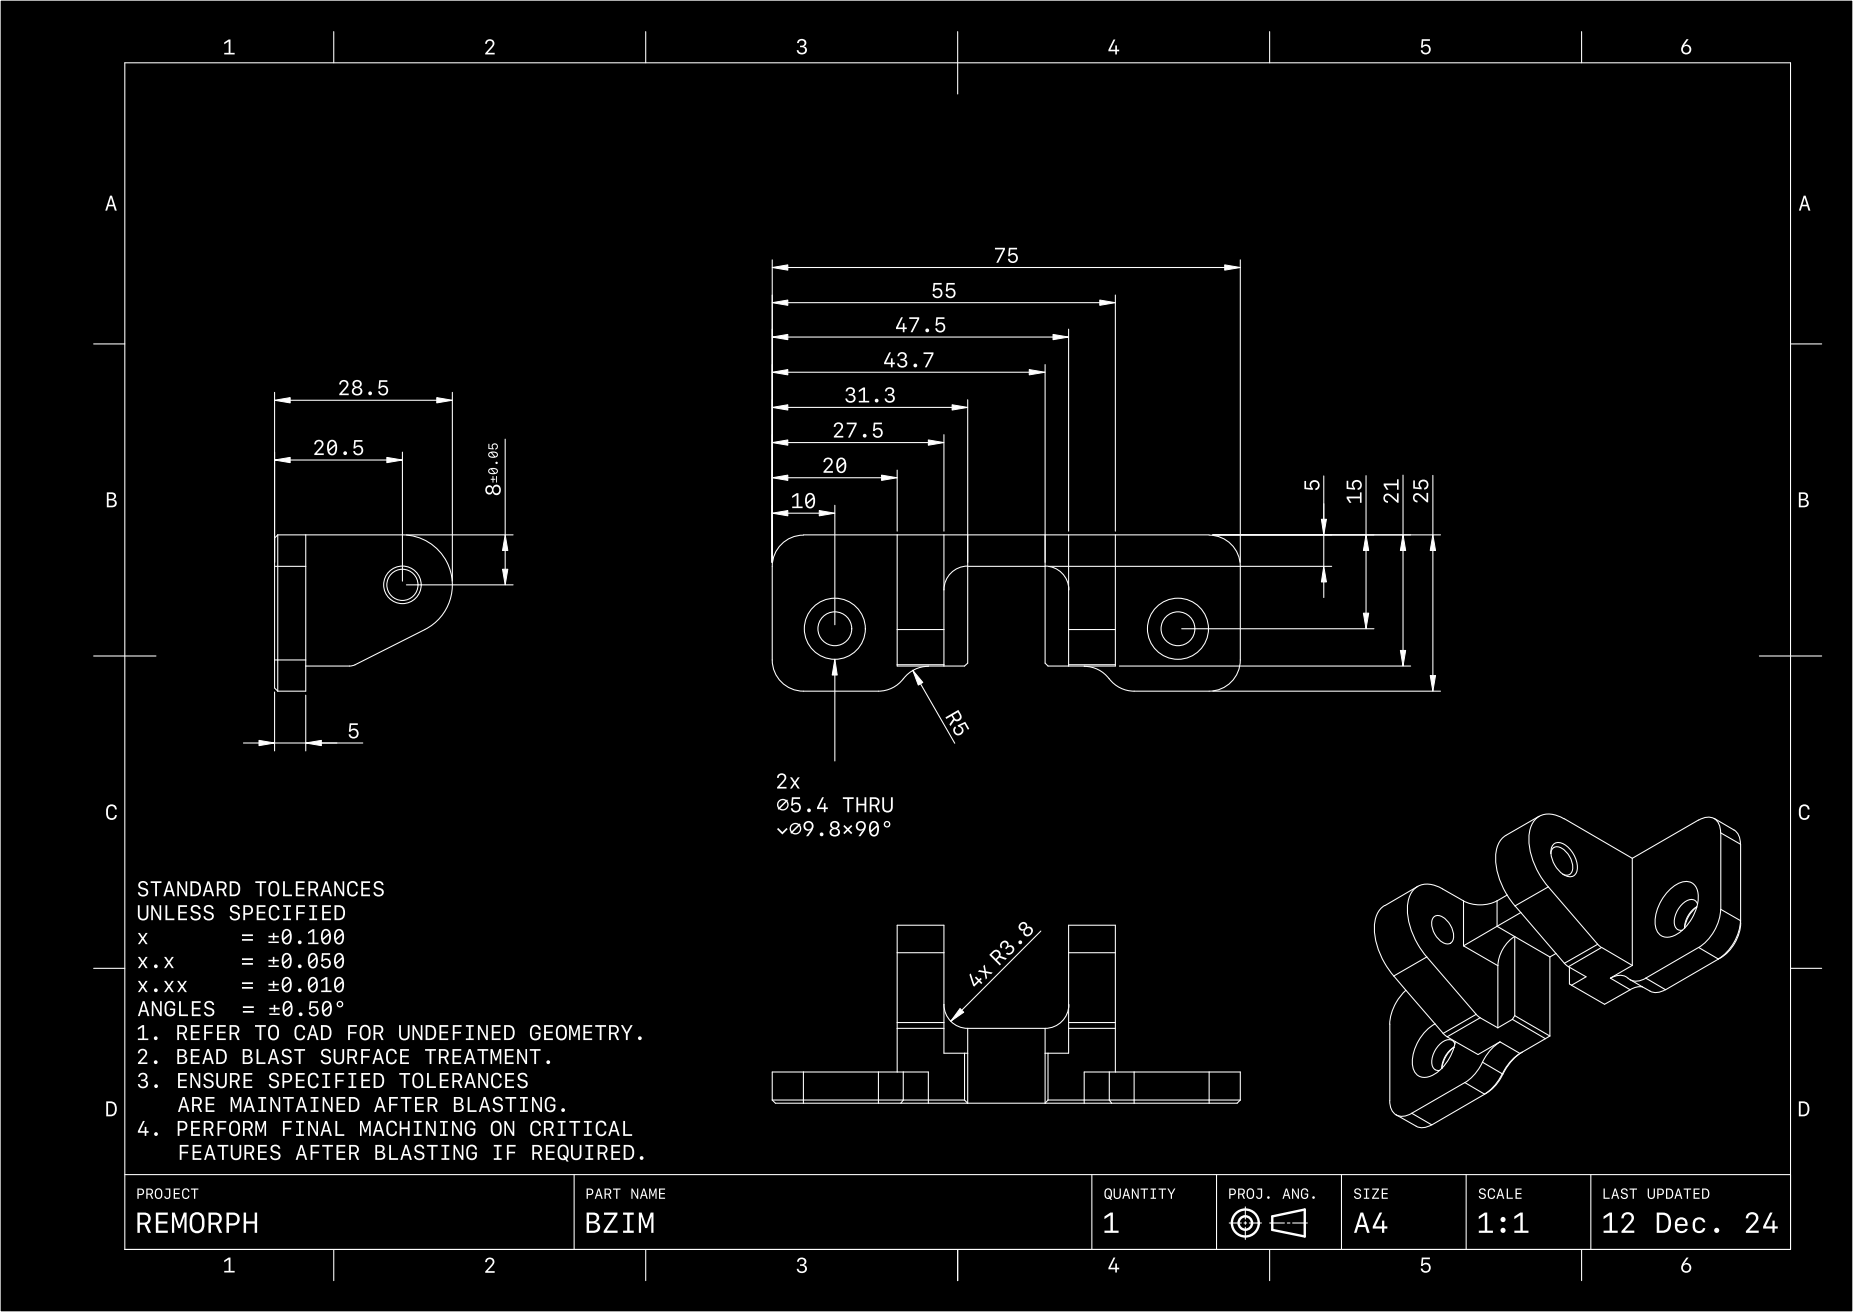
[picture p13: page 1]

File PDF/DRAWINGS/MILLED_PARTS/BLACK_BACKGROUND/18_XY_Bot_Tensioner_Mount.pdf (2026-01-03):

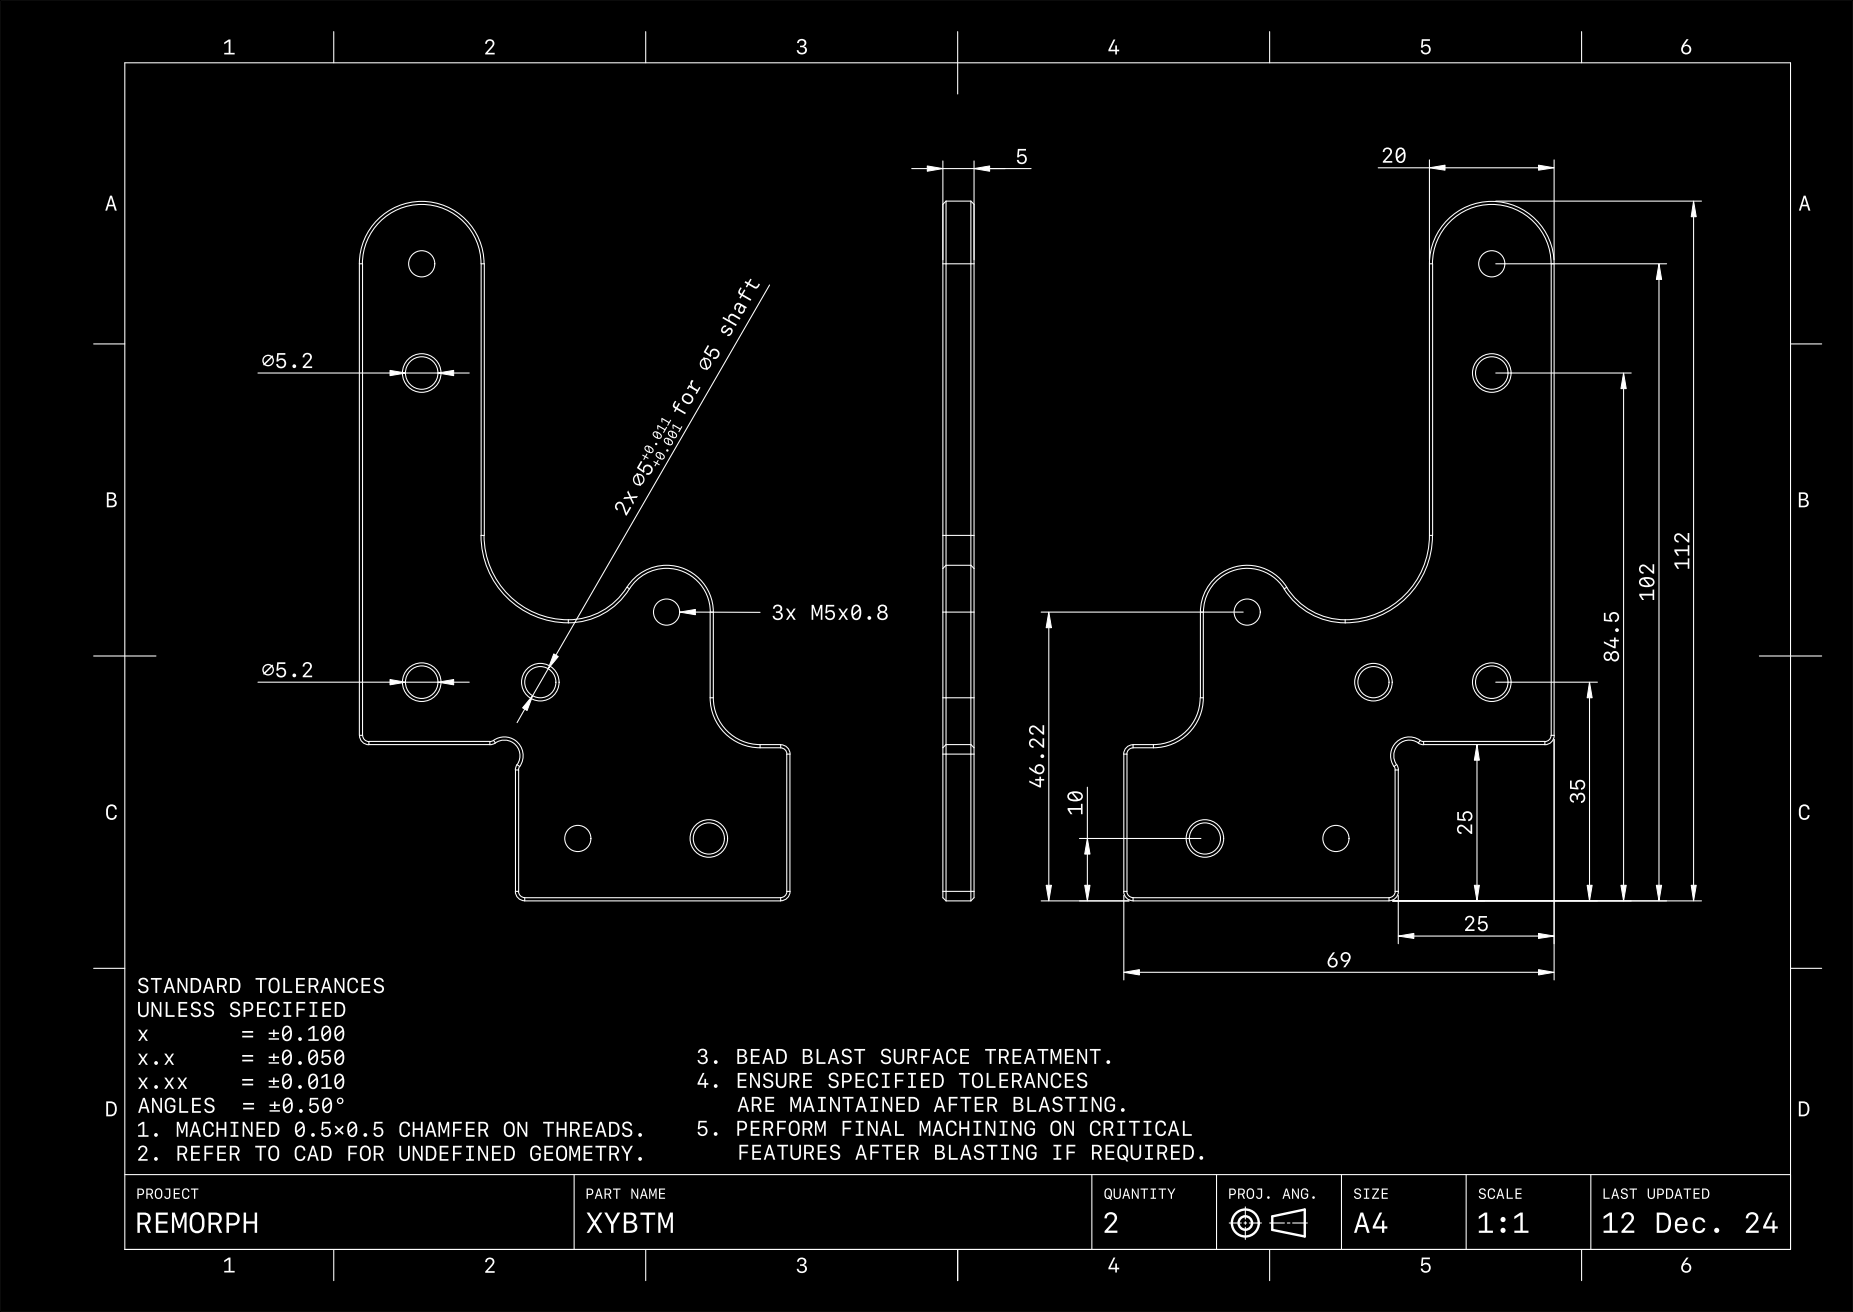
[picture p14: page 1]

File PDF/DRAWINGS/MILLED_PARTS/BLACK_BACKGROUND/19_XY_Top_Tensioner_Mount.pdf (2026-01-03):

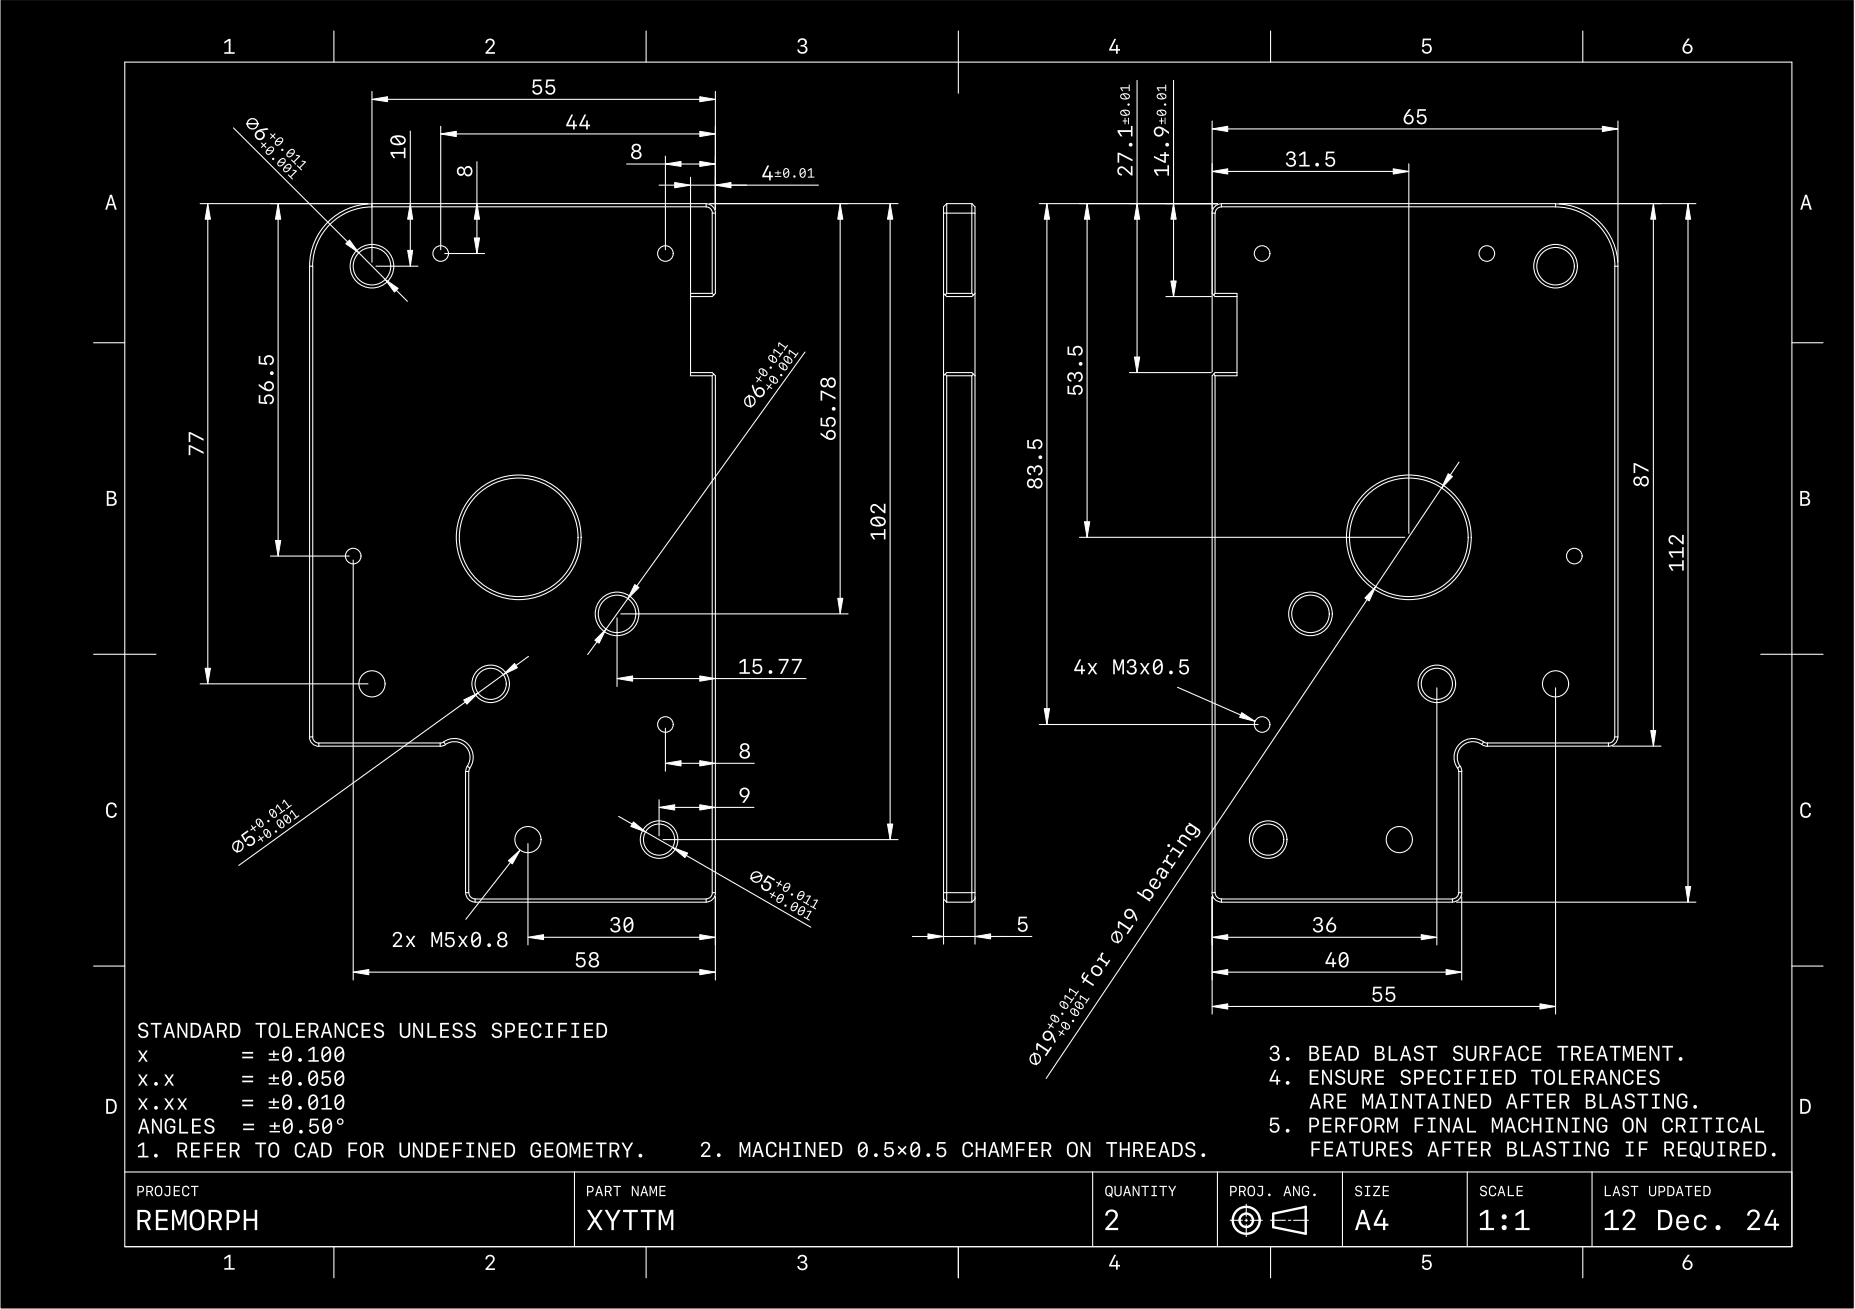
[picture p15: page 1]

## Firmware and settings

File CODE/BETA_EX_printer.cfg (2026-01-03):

##########################################
#                REMORPH                 #
##########################################

# System configuration for:
# 1: Recore A8
# 2: EBB42 V1.2 STM2G0B1 (Toolhead)
# 3: EBB42 V1.2 STM2G0B1 (Replexus)
# 4: Beacon 3D Sensor
#
# Compiling firmware for: 
# = AR100 and STM32F031 (Recore A8)
# = wiki.iagent.no/wiki/Rebuild_v1.0.2


##########################################
#                 MCU'S                  #
##########################################

# STM32F031 mcu
[mcu]
serial: /dev/ttyS2
baud: 250000
restart_method: command

# AR100 mcu
[mcu ar100]
serial: /dev/ttyS1
baud: 1500000

# Toolhead EBB42 mcu
[mcu toolhead]
#serial: /dev/serial/by-id/usb-Klipper_stm32g0b1xx_1B0042000B504D4D35383820-if00
restart_method: command

# Replexus EBB42 mcu
[mcu replexus]
#serial: /dev/serial/by-id/usb-Klipper_stm32g0b1xx_07003F000B504D4D35383820-if00
restart_method: command

# Recore board Temp Sensor
[temperature_sensor Recore_Board]
sensor_type: EPCOS 100K B57560G104F
sensor_pin: PA6
min_temp: 0
max_temp: 100
gcode_id: board

# Recore A64 Temp
[temperature_sensor Recore_A64_AR100]
sensor_type: temperature_host
min_temp: 0
max_temp: 100
gcode_id: soc

# TH EBB MCU Temp
[temperature_sensor Toolhead_EBB42]
sensor_type: temperature_mcu
sensor_mcu: toolhead
min_temp: 0
max_temp: 100

# Replexus EBB MCU Temp
[temperature_sensor Replexus_EBB42]
sensor_type: temperature_mcu
sensor_mcu: replexus
min_temp: 0
max_temp: 100

[beacon]
#serial: /dev/serial/by-id/usb-Beacon_Beacon_RevH_6C1D27425154354D38202020FF0A082D-if00
x_offset: 0
y_offset: 30
mesh_main_direction: x
mesh_runs: 2
home_xy_position: 153.5,153.5   # Matches your safe_z_home and previous cal position
home_z_hop: 5                   # Lift nozzle 5mm before/after XY moves (prevents dragging)
home_z_hop_speed: 30            # Speed for the hop
home_xy_move_speed: 333         # Fast XY travel to homing position
home_method: contact            # Use "contact" mode for reliable first homing (slow dive + touch)
home_method_when_homed: proximity  # Switch to fast proximity (eddy current) after initial home/cal
home_autocalibrate: unhomed     # Auto-run calibration on first/unhomed G28 only (perfect for fresh setups)

#

##########################################
#                 PRINTER                #
##########################################

[printer]
kinematics: corexy
max_velocity: 1000
max_accel: 125000
max_z_velocity: 50
max_z_accel: 300

[temperature_sensor Chamber]
sensor_type: PT1000
sensor_pin: replexus:PA3
pullup_resistor: 4670
min_temp: 0
max_temp: 100
gcode_id: chamber

[output_pin print_fan]
pin: replexus:PD3
pwm: true
cycle_time: 0.001
shutdown_value: 0

[output_pin chamber_fan]
pin: replexus:PB8
pwm: true
cycle_time: 0.001
shutdown_value: 1

[temperature_sensor Electronics]
sensor_type: PT1000
sensor_pin: PA0
pullup_resistor: 4795
min_temp: 0
max_temp: 100

[fan_generic Electronics_fan]
pin: PA8
max_power: 1.0
shutdown_speed: 0.0
min_power: 0.125
cycle_time: 0.00004

[gcode_macro _ELECTRONICS_FAN_CONTROL]
gcode:
  {% set board_temp = printer["temperature_sensor Recore_Board"].temperature|float %}
  {% set bay_temp  = printer["temperature_sensor Electronics"].temperature|float %}

  {% set low_temp  = 35.0 %}
  {% set high_temp = 65.0 %}

  # Override if Recore board exceeds threshold
  {% if board_temp >= 69.0 %}
    SET_GCODE_VARIABLE MACRO=_EMERGENCY_FAN_RAMP VARIABLE=active VALUE=1
    _EMERGENCY_FAN_RAMP
  {% else %}
    # Cancel emergency ramp when board cools
    SET_GCODE_VARIABLE MACRO=_EMERGENCY_FAN_RAMP VARIABLE=active VALUE=0

    # Standard bay temperature control
    {% if bay_temp < low_temp %}
      SET_FAN_SPEED FAN=Electronics_fan SPEED=0
    {% else %}
      {% set fraction = (bay_temp - low_temp) / (high_temp - low_temp) %}
      {% set speed = [fraction, 0.5]|min %}
      {% set speed = [speed, 0.0]|max %}
      SET_FAN_SPEED FAN=Electronics_fan SPEED={ speed }
    {% endif %}
  {% endif %}

[gcode_macro _EMERGENCY_FAN_RAMP]
variable_active: 0      # 1 = emergency mode active
variable_step:   0      # current step counter (0-200)
gcode:
  {% if active %}
    {% set total_steps = 200 %}
    {% set step = step|int %}
    {% if step < 100 %}
      # Ramp-up phase: 0 → 100 %
      {% set speed = (step / 100.0)|float %}
    {% elif step < 200 %}
      # Ramp-down phase: 100 → 0 %
      {% set speed = 1.0 - ((step - 100) / 100.0)|float %}
    {% else %}
      # Cycle complete
      {% set speed = 0.0 %}
    {% endif %}

    
    SET_FAN_SPEED FAN=Electronics_fan SPEED={ speed }
    
    {% set next_step = step + 1 %}
    SET_GCODE_VARIABLE MACRO=_EMERGENCY_FAN_RAMP VARIABLE=step VALUE={ next_step }
    UPDATE_DELAYED_GCODE ID=_EMERGENCY_RAMP_LOOP DURATION=1
  {% else %}
    # Emergency ended: reset and stop
    SET_FAN_SPEED FAN=Electronics_fan SPEED=0
    SET_GCODE_VARIABLE MACRO=_EMERGENCY_FAN_RAMP VARIABLE=step VALUE=0
    UPDATE_DELAYED_GCODE ID=_EMERGENCY_RAMP_LOOP DURATION=0
  {% endif %}

[delayed_gcode _EMERGENCY_RAMP_LOOP]
gcode:
  _EMERGENCY_FAN_RAMP

[delayed_gcode ELECTRONICS_FAN_LOOP]
initial_duration: 1.0
gcode:
  _ELECTRONICS_FAN_CONTROL
  UPDATE_DELAYED_GCODE ID=ELECTRONICS_FAN_LOOP DURATION=60

[resonance_tester]
accel_chip: beacon
probe_points: 153.5, 153.5, 152

#[temperature_sensor BME680]
#sensor_type: BME280
#i2c_mcu: replexus
#i2c_software_scl_pin: replexus:PB3
#i2c_software_sda_pin: replexus:PB4
#i2c_speed: 100000
#i2c_address: 119

# Optional for VOC/gas readings:
# gas_heater_temperature: 320
# gas_heater_duration: 150

[gcode_macro QUERY_BME280]
gcode:
    {% set sensor = printer["bme280 my_sensor"] %}
    {action_respond_info(
        "Temperature: %.2f C\n"
        "Pressure: %.2f hPa\n"
        "Humidity: %.2f%%" % (
            sensor.temperature,
            sensor.pressure,
            sensor.humidity))}

#

##########################################
#                 LIGHT                  #
##########################################

# Pin Definition
[output_pin replexus_led]
pin: replexus:PB13
pwm: True
cycle_time: 0.0005
scale: 100

# Startup Brightness 42%
[delayed_gcode led_startup_42]
initial_duration: 1
gcode:
    SET_PIN PIN=replexus_led VALUE=42

# Dim to 5% after 42 min of inactivity
[idle_timeout]
timeout: 2520 # 42 minutes (42 * 60 = 2520 seconds)
gcode:
    SET_PIN PIN=replexus_led VALUE=5

# Resume Brightness 42%
[gcode_macro Light]
gcode:
    SET_PIN PIN=replexus_led VALUE=42

#

##########################################
#               X/Y SERVOS               #
##########################################

# X Axis
[stepper_x]
step_pin: ar100:PL10
dir_pin: ar100:PE14
rotation_distance: 20
microsteps: 1
full_steps_per_rotation: 2000
endstop_pin: !toolhead:PB6
position_endstop: 313
position_max: 313
position_min: 3
homing_speed: 100
homing_retract_dist: 7

# Y Axis
[stepper_y]
step_pin: ar100:PL11
dir_pin: !ar100:PE15 
rotation_distance: 20
microsteps: 1
full_steps_per_rotation: 2000
endstop_pin: !replexus:PB6
position_endstop: 372.6
position_max: 372.6
position_min: 3.6
homing_speed: 100
homing_retract_dist: 7

##########################################
#                 Z Axis                 #
##########################################

#[safe_z_home]
#home_xy_position: 153.5 , 153.5
#z_hop: 3

[bed_mesh]
speed: 200
horizontal_move_z: 10
mesh_min: 30, 40
mesh_max: 247, 247
probe_count: 30, 30
algorithm: bicubic
fade_start: 1
zero_reference_position: 153.5, 153.5

[tmc2209 stepper_z]
uart_pin: ar100:PE16
uart_address: 0
run_current: 0.800
hold_current: 0.800
stealthchop_threshold: 999999
sense_resistor: 0.110

[stepper_z]
step_pin: ar100:PL4
dir_pin: ar100:PE8
endstop_pin: probe:z_virtual_endstop
rotation_distance: 20
gear_ratio: 5:1
microsteps: 16
position_max: 304
homing_speed: 50.0
homing_retract_dist: 7.0

[tmc2209 stepper_z1]
uart_pin: ar100:PE16
uart_address: 1
run_current: 0.800
hold_current: 0.800
stealthchop_threshold: 999999
sense_resistor: 0.110

[stepper_z1]
step_pin: ar100:PL5
dir_pin: !ar100:PE9
rotation_distance: 20
gear_ratio: 5:1
microsteps: 16


[tmc2209 stepper_z2]
uart_pin: ar100:PE16
uart_address: 2
run_current: 0.800
hold_current: 0.800
stealthchop_threshold: 999999
sense_resistor: 0.110

[stepper_z2]
step_pin: ar100:PL6
dir_pin: ar100:PE10
rotation_distance: 20
gear_ratio: 5:1
microsteps: 16


[z_tilt]
z_positions:
   26,79.89         # Position for Stepper Z1
   281,79.89        # Position for Stepper Z2
   153.5,300.72     # Position for Stepper Z3
points:
   26,49.89        # Probe point near stepper_z
   281,49.89       # Probe point near stepper_z1
   153.5,270.72     # Probe point near stepper_z2 (safe on-bed location)
speed: 300
horizontal_move_z: 5
retries: 5
retry_tolerance: 0.01

##########################################
#                EXTRUDERS               #
##########################################
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
